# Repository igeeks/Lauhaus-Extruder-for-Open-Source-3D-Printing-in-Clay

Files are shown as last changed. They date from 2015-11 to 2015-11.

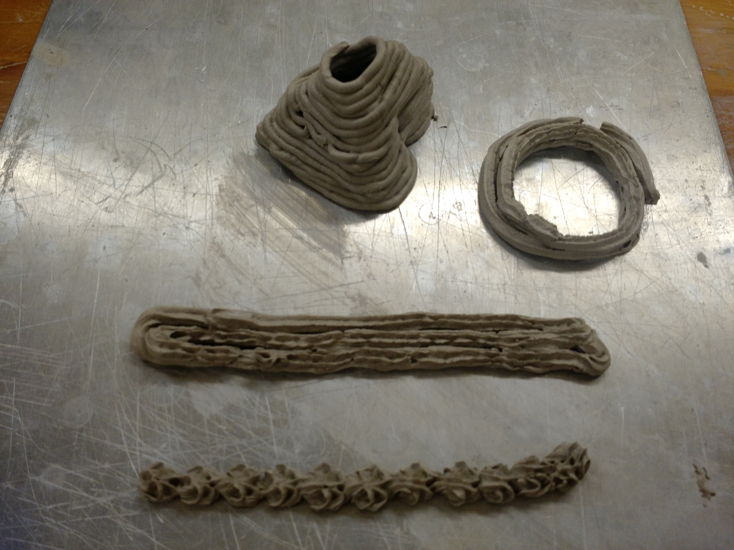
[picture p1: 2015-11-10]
Version 0.2_1 (uses Frosting Tip)/Images/IMG_20151110_134412253.jpg

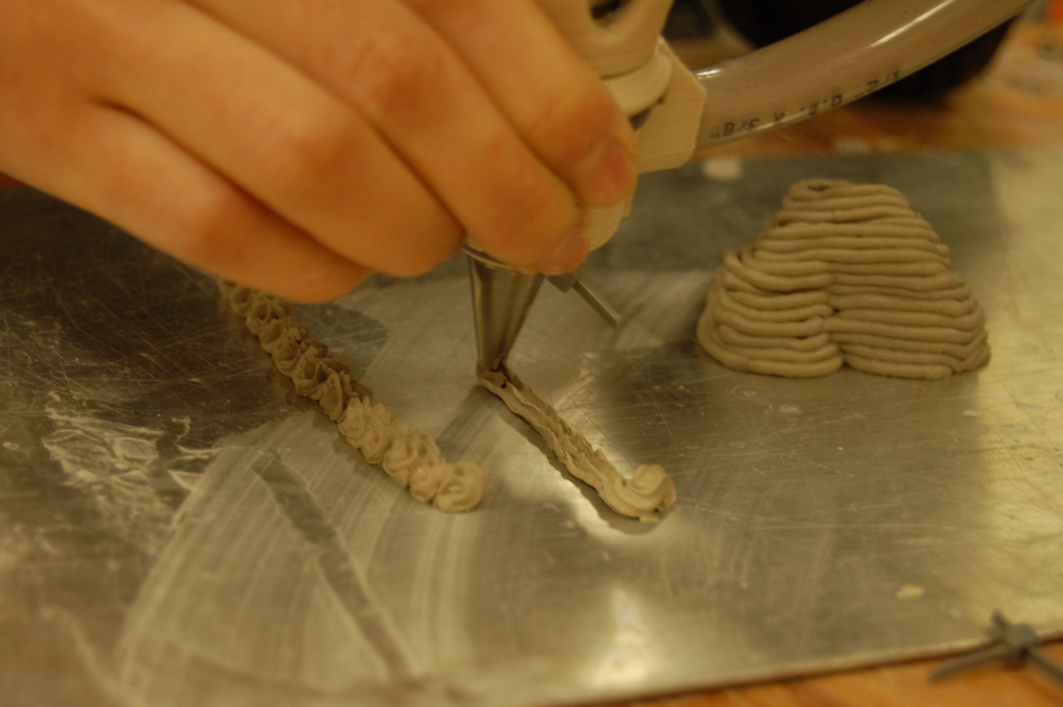
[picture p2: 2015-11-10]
Version 0.2_1 (uses Frosting Tip)/Images/DSC_0014.JPG

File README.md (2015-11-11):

# Lauhaus-Extruder-for-Open-Source-3D-Printing-in-Clay
An Open Source 3D print head for printing clay and perhaps other pastes & fluids

Fist of all, many thanks to people who have been pioneering open source 3d printing in clay. Notably Dries Verbruggen of Unfold Studio, Jonathan Keep of the "Build Your Own Ceramic Delta Printer", WASP Project - a 3D printer company based in Italy doing remarkable work, and Richard Horne "RichRap3D" whose open source paste extruder was the first RepRap clay extruder I came across.

The design here draws inspiration and conceptual direction from all of those individuals listed and some others too. This project is intended to be as low-cost as possible and also as easy to assemble and use as possible. It tries to be reliant on parts which are widely available or 3d printable. 

This project is being developed by students of Engineering and students of Art at Penn State University. The project receives support from Penn State's Learning Factory program: http://www.lf.psu.edu/ . The project is being led by Tom Lauerman, an artist & teacher with an interest in 3D printing, clay, design, engineering, bicycles, eating ice cream, playing drums poorly, and other activities. http://www.tomlauerman.com/

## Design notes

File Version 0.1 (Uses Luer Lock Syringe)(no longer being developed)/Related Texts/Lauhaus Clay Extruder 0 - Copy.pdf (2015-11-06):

## Lauhaus Clay Extruder 0.1 Bill of Materials

with helpful links and counterproductive observations

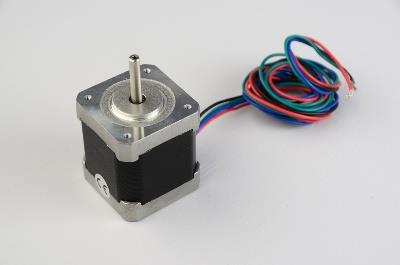
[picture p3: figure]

One Nema 17 Motor – the most common motor used in RepRap printers. Available in many locations. I buy mine from Lulzbot: https://www.lulzbot.com/products/nema-17-stepper-motor . These can also sometimes be found inside of old document scanners if you like breaking things.

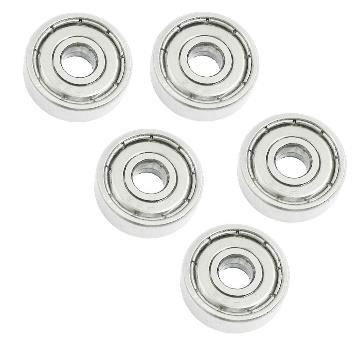
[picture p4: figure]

One 625ZZ Bearing 5mm x 5mm x 16mm – These are very common in skateboard wheels and are very cheap – usually less than 1 dollar per. Should be in stock at your local skate shop. Also at Amazon: http://www.amazon.com/Skateboard-Groove-Radial-Bearings-625ZZ/dp/B009EPNW8Y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 (http://www.amazon.com/Skateboard-Groove-Radial-Bearings-625ZZ/dp/B009EPNW8Y?s=industrial)

One wood screw. The first one I tried was 14 guage (1/4inch diameter (6.3mm metric)) and was three inches long. I cut the head off with a dremel cut off wheel. This screw worked, but I’m certain there ae better augers out there. I plan to experiment with a range of screws, drill bits, etc. Also I’m not sure why something labeled ¼” (6.3mm) was able to fit in the bearing’s 5mm hole. I sanded it a bit, but not that much. I think screws are highly variable by manufacturer and that their dimensions are sometimes more nominal than actual – at least in my neck of the woods. Here’s one similar to mine. (https://www.fastenal.com/products/details/1130238)

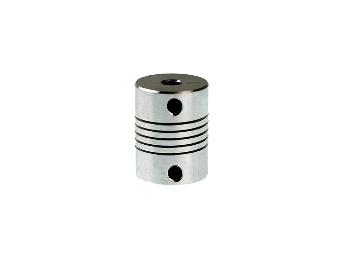
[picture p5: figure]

One flexible coupler. – 5mm holes – This attaches the screw to the motor shaft. These can be purchased online, here’s where mine came from. (https://www.inventables.com/technologies/flexible-coupler) That said, I always liked the way the Prusa i3 printer originally used a piece of tubing instead of a coupler. (http://3.bp.blogspot.com/-Z1Y2iyhLs8A/UhL_BsgxiFI/AAAAAAAAF6w/BmKeCiHRCiw/s1600/Prusai3-metalframe.jpg) So maybe this coupler is a bit too esoteric for my design – it may not be necessary – I’m going to try alternatives.

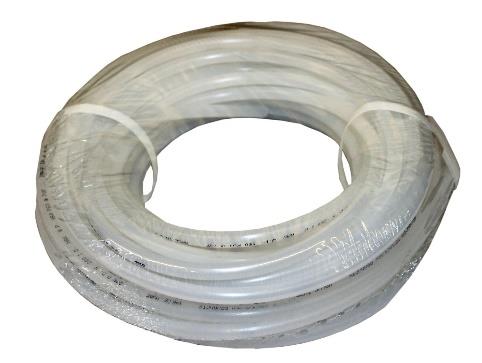
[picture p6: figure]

Flexible tubing (to from feed tank to extruder head) I used some that had an inside diameter of 3/8” and an outside diameter of ½”. The WASP project uses 12mm tubing, which I’m guessing is essentially the exact same diameter. I used regular plastic tubing from the local hardware store. This was a bad choice! The WASP project uses Teflon (ptfe) tubing – which I’m sure significantly reduces drag on the clay moving through the tube. I’m going to buy some Teflon tube from here. (http://www.mcmaster.com/#5033k35/=zp269m) Actually, on second thought, that is annoyingly expensive tubing. I may go over to the part of my campus where the cows are kept and milked (hundreds of them) and ask around about what type of tubing has the least friction. Then I’m going to get Ice Cream.

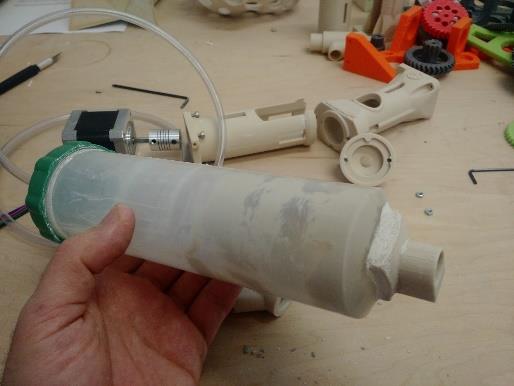
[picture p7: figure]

Clay holding/Feed tank. I repurposed this one from the Jonathan Keep printer bill of materials. I cut off the luer lock syringe tip, drilled the hole out to ½ inch and 3d printed anew nozzle fitting for it which I epoxied on with PC-11 epoxy. This is not an ideal solution! I mean it worked fine, but its smallish and why buy a thing just to cut it up and glue printed parts to? Look how nice the WASP project tank is (lower right):

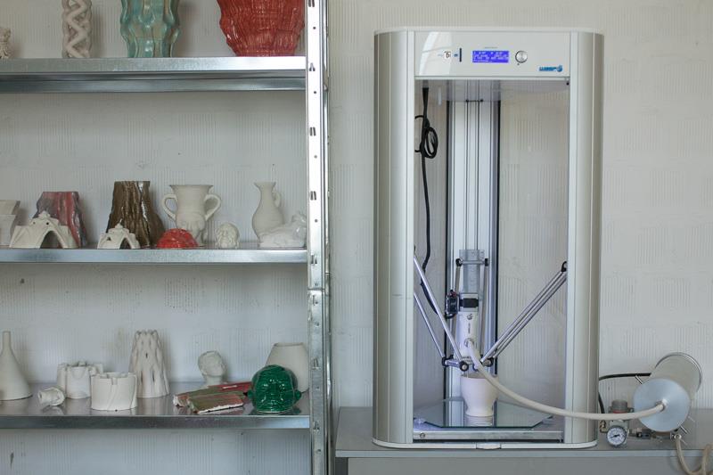
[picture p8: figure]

That said, I actually have a grudge against the pneumatic holding tank aspect of the project. I really want to design and build a mechanical tank – a stepper motor driven plunger. For two reasons:

1. To be able to modulate feed rate and pressure via software/firmware.
2. Air compressors are expensive, large, and noisy.

More on this later – but eliminating all compressed air from the system is a goal of mine.

That’s everything (+ the three 3d printed parts (extruder shell, extrude cap, part that does the work).

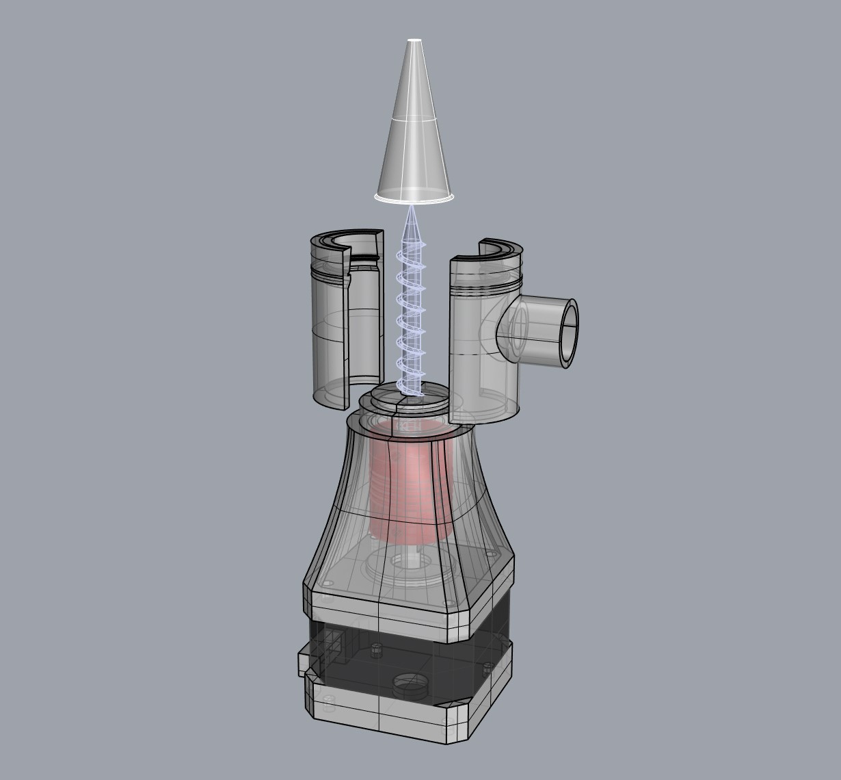
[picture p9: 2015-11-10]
Version 0.2_1 (uses Frosting Tip)/Images/Clay Extruder 02.jpg

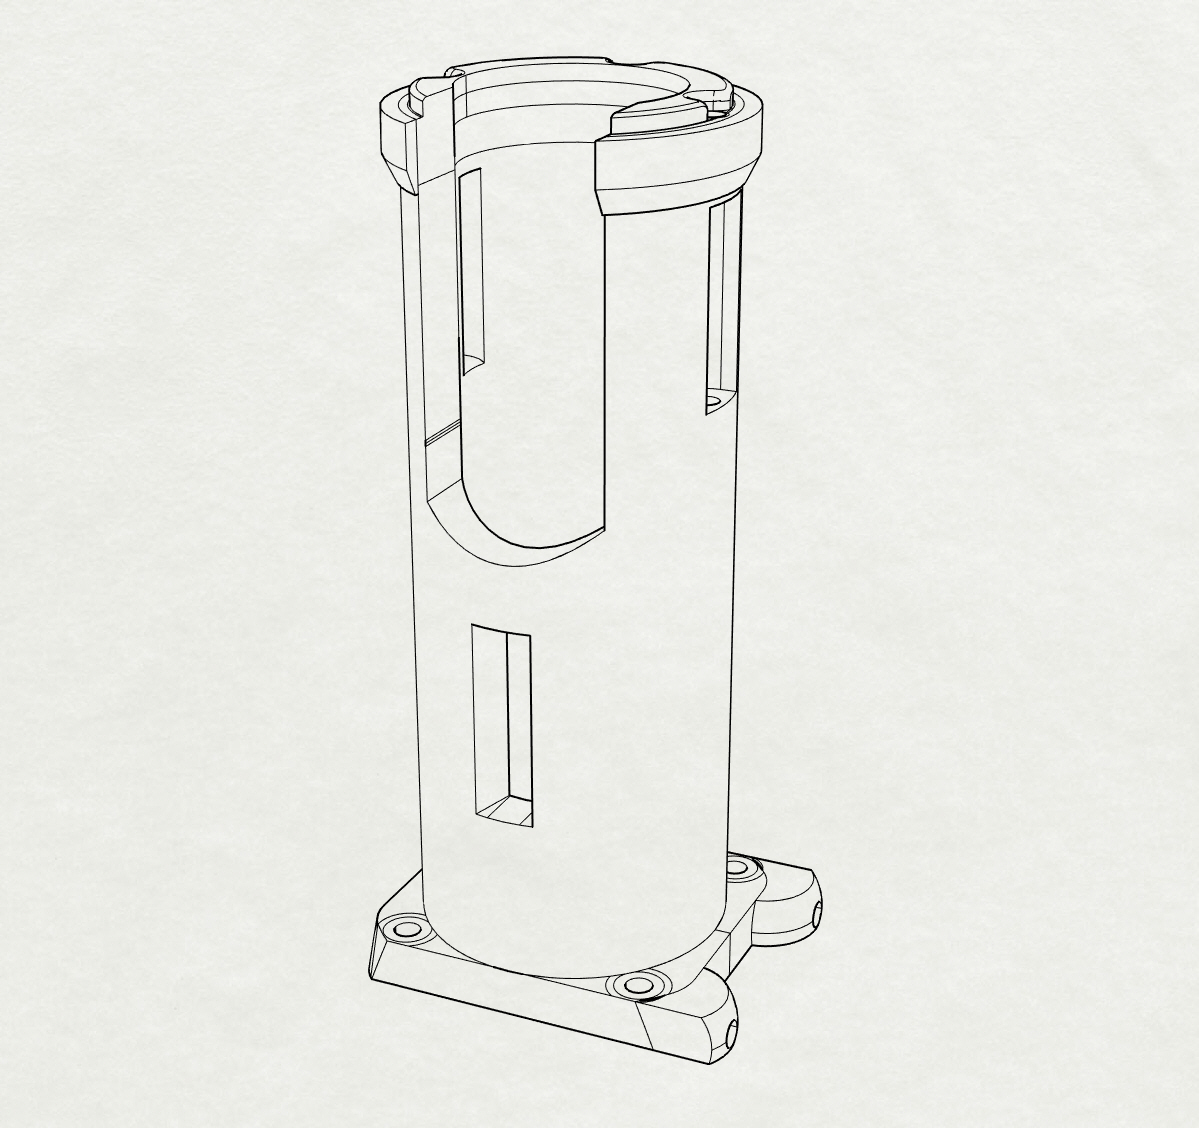
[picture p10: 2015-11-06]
Version 0.1 (Uses Luer Lock Syringe)(no longer being developed)/JPG Files/Lauhaus Extuder Shell.jpg

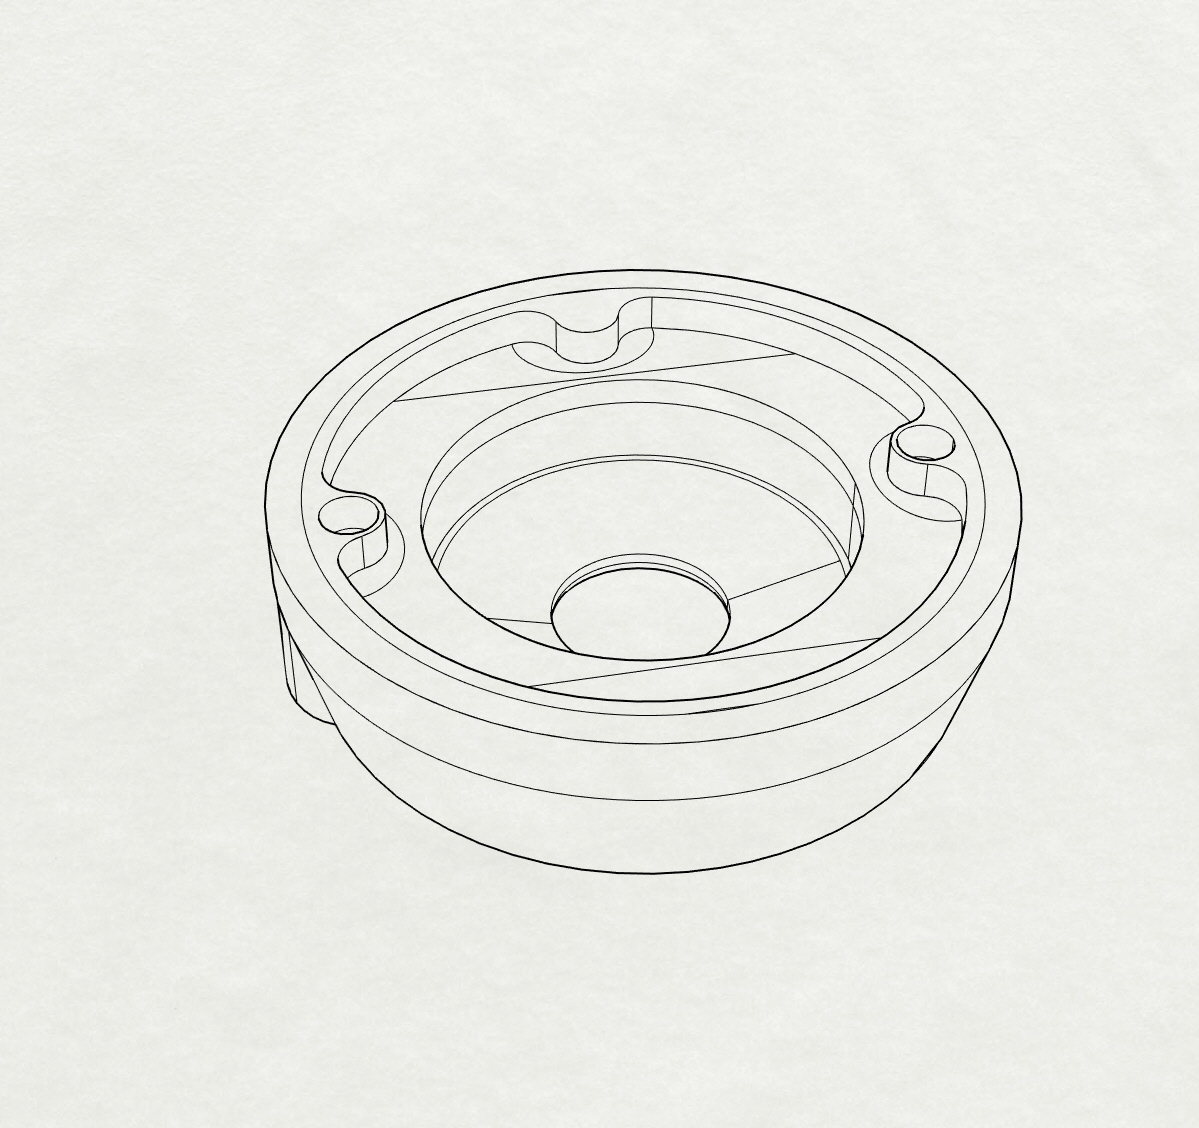
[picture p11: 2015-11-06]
Version 0.1 (Uses Luer Lock Syringe)(no longer being developed)/JPG Files/Lauhaus Extuder Cap.jpg

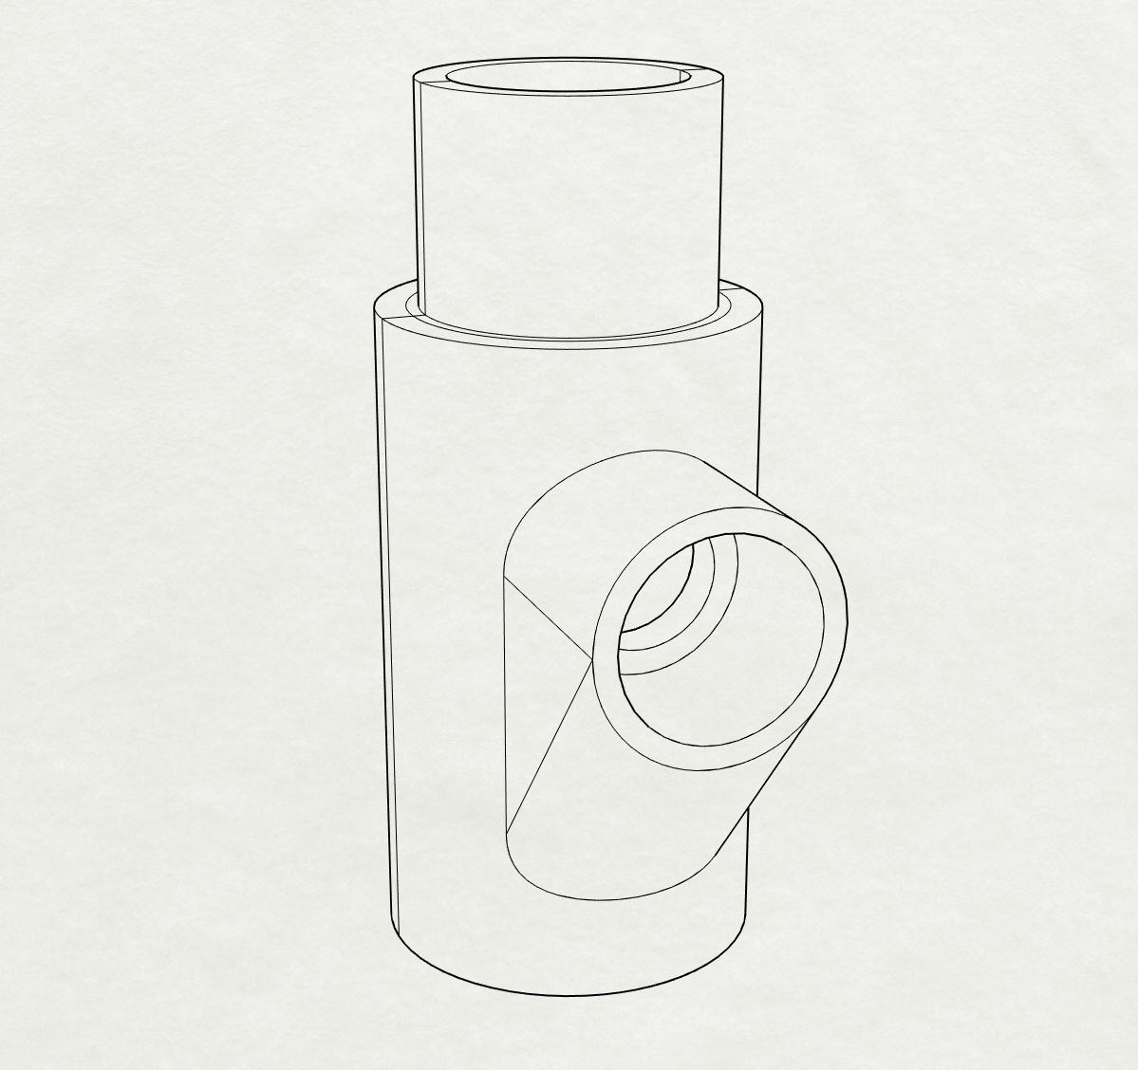
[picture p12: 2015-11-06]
Version 0.1 (Uses Luer Lock Syringe)(no longer being developed)/JPG Files/Lauhuas Extruder Part Which Does The Work.jpg

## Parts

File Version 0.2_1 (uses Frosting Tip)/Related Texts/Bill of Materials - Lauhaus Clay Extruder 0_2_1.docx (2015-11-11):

Lauhaus Clay Extruder 0.2_1 Bill of Materials

with helpful links and counterproductive observations

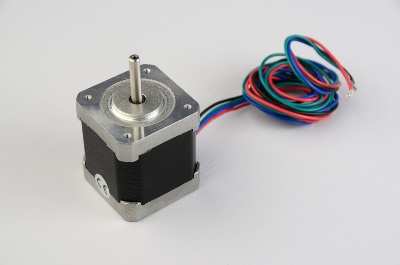
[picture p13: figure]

$13.95

One Nema 17 Motor – the most common motor used in RepRap printers. Available in many locations. I buy mine from Lulzbot: https://www.lulzbot.com/products/nema-17-stepper-motor . These can also sometimes be found inside of old document scanners if you like breaking things.

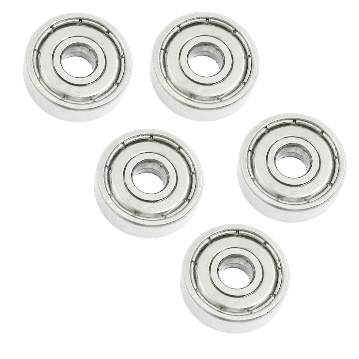
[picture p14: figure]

$1.00 (approx.)

One 625ZZ Bearing 5mm x 5mm x 16mm – These are very common in skateboard wheels and are very cheap – usually less than 1 dollar per. Should be in stock at your local skate shop. Also at Amazon: http://www.amazon.com/Skateboard-Groove-Radial-Bearings-625ZZ/dp/B009EPNW8Y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

$0.69

One screw. I used a “Timber Tite ¼” x 4” Deck Screw I purchased from my local hardware store. I cut the head off using a Dremel cut-off wheel. http://wedo.hillmangroup.com/item/all-categories/timbertite-trade-landscape-screw/47804

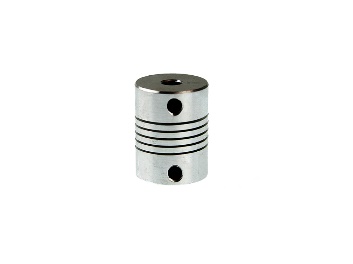
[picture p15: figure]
Flexible Coupler

$2.99

One flexible coupler. – 5mm holes – This attaches the screw to the motor shaft. These can be purchased online, here’s where mine came from (https://www.inventables.com/technologies/flexible-coupler). Here’s a cheaper that I’m sure works just as well (http://www.ebay.com/itm/Flexible-Shaft-Coupler-5mm-To-5mm-CNC-Mill-Router-Reprap-Prusa-i3-3D-printer-/121485418717). That said, I always liked the way the Prusa i3 printer originally used a piece of tubing instead of a coupler (http://3.bp.blogspot.com/-Z1Y2iyhLs8A/UhL_BsgxiFI/AAAAAAAAF6w/BmKeCiHRCiw/s1600/Prusai3-metalframe.jpg). So maybe this coupler is a bit too esoteric for my design – it may not be necessary – I’m going to try alternatives.

Total extruder cost: $18.63

Feed System Items

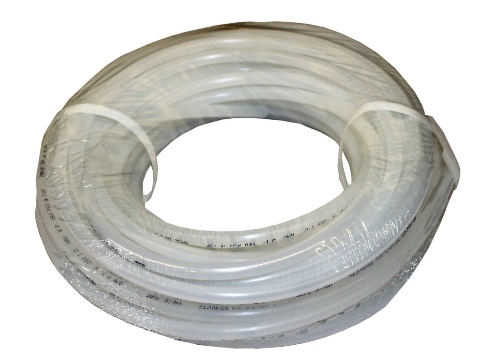
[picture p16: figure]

Flexible tubing (to from feed tank to extruder head) I used some that had an inside diameter of 3/8” and an outside diameter of ½”. The WASP project uses 12mm tubing, which I’m guessing is essentially the exact same diameter. I used regular plastic tubing from the local hardware store. This was a bad choice! The WASP project uses Teflon (ptfe) tubing – which I’m sure significantly reduces drag on the clay moving through the tube. I’m going to buy some Teflon tube from here (http://www.mcmaster.com/). Actually, on second thought, that is annoyingly expensive tubing. I may go over to the part of my campus where the cows are kept and milked (hundreds of them) and ask around about what type of tubing has the least friction. Then I’m going to get Ice Cream.

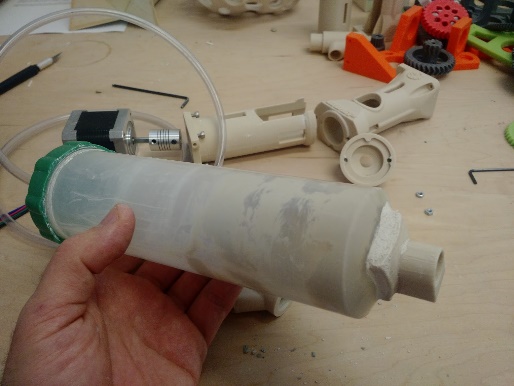
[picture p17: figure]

Clay holding/Feed tank. I repurposed this one from the Jonathan Keep printer bill of materials. I cut off the luer lock syringe tip, drilled the hole out to ½ inch and 3d printed anew nozzle fitting for it which I epoxied on with PC-11 epoxy. This is not an ideal solution! I mean it worked fine, but its smallish and why buy a thing just to cut it up and glue printed parts to? Look how nice the WASP project tank is (lower right):

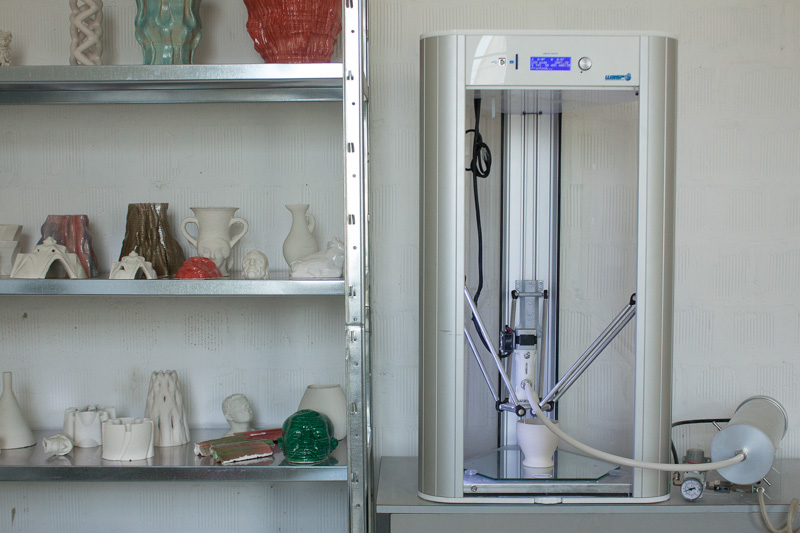
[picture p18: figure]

That said, I actually have a grudge against the pneumatic holding tank aspect of the project. I really want to design and build a mechanical tank – a stepper motor driven plunger. For two reasons:

1. To be able to modulate feed rate and pressure via software/firmware.
2. Air compressors are expensive, large, and noisy.

More on this later – but eliminating all compressed air from the system is a goal of mine.

That’s everything (+ the three 3d printed parts (extruder shell, extrude cap, part that does the work).

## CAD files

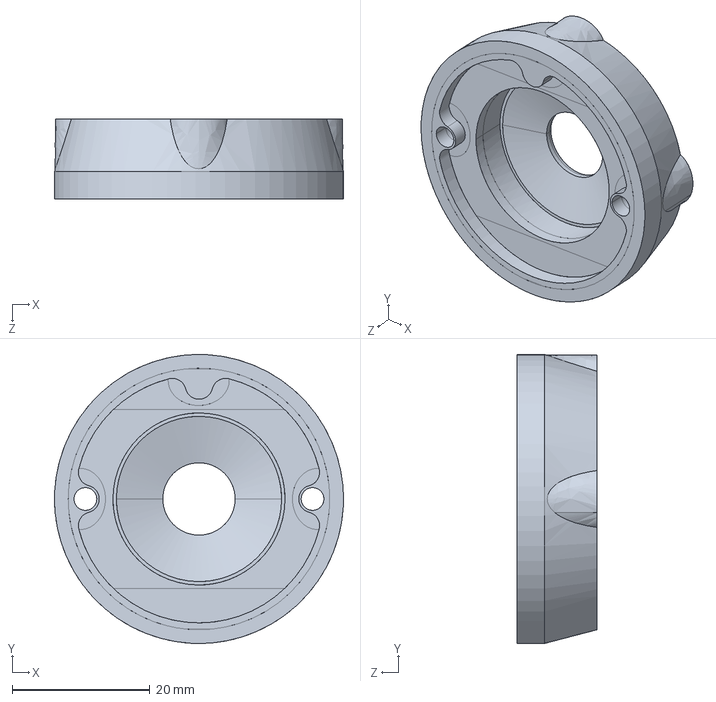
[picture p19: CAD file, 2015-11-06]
Version 0.1 (Uses Luer Lock Syringe)(no longer being developed)/IGES Files/Lauhaus Extruder Cap.igs
42.0 x 42.0 x 11.7 mm

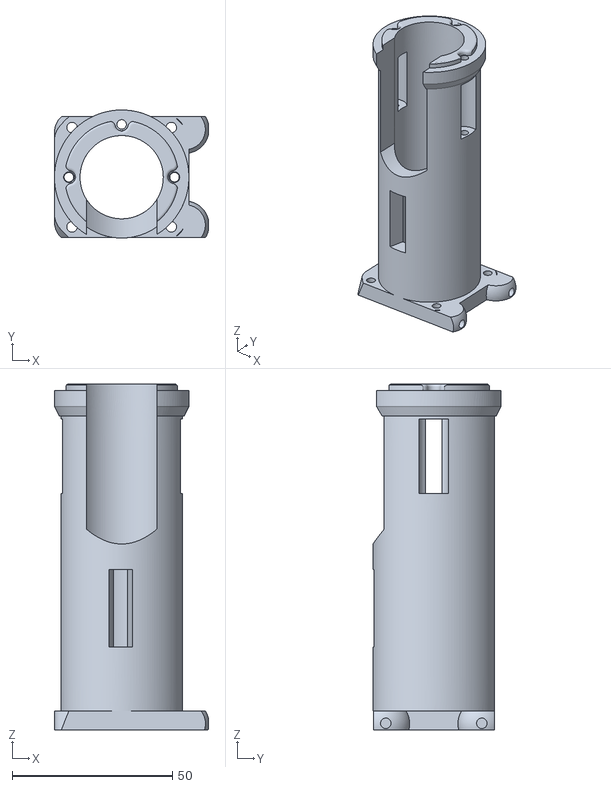
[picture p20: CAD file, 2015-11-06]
Version 0.1 (Uses Luer Lock Syringe)(no longer being developed)/STL Files/Lauhaus Extruder Shell.stl
48.1 x 40.0 x 108.1

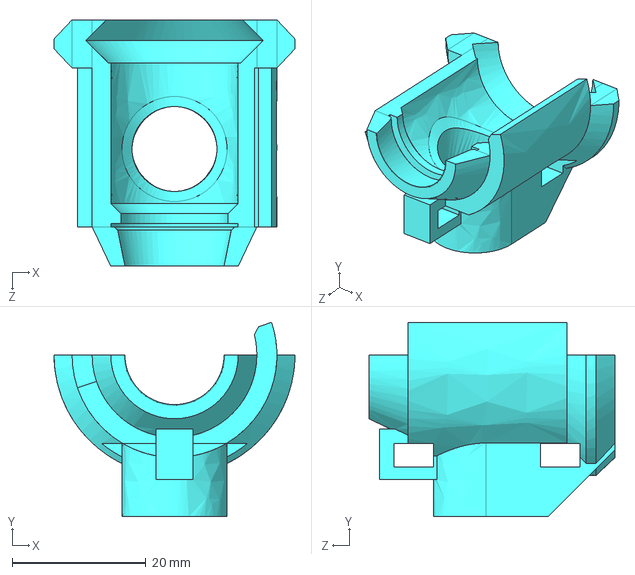
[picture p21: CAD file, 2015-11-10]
Version 0.2_1 (uses Frosting Tip)/IGES Files/Lauhaus Clay Extruder Side A 0_2_1.igs
36.0 x 29.1 x 36.9 mm

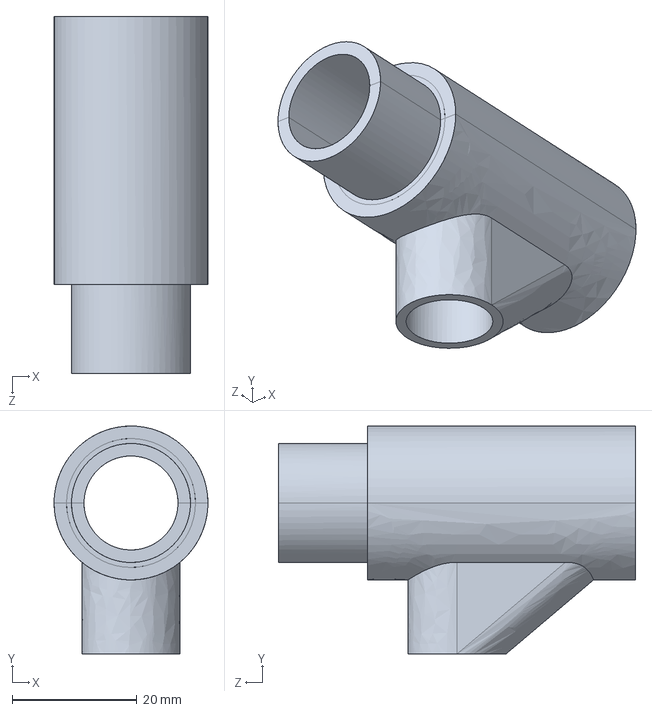
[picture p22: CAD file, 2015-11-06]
Version 0.1 (Uses Luer Lock Syringe)(no longer being developed)/IGES Files/Lauhaus Extruder Part Which Does The Work.igs
24.6 x 36.5 x 57.2 mm

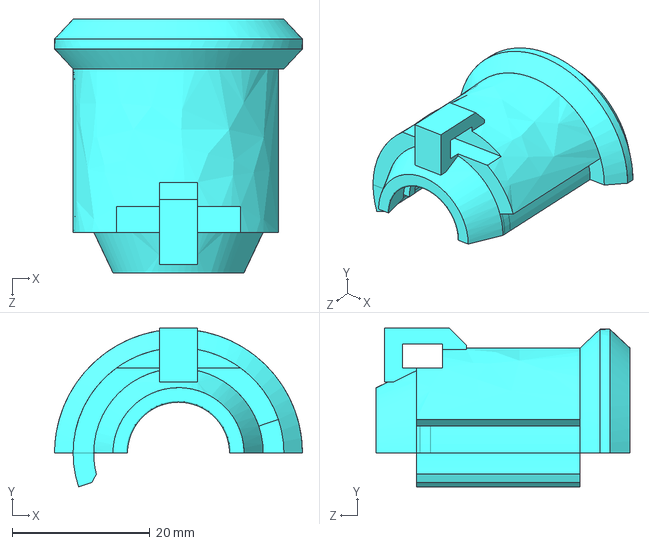
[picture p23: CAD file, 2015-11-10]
Version 0.2_1 (uses Frosting Tip)/IGES Files/Lauhaus Clay Extruder Side B 0_2_1.igs
36.0 x 23.1 x 36.9 mm

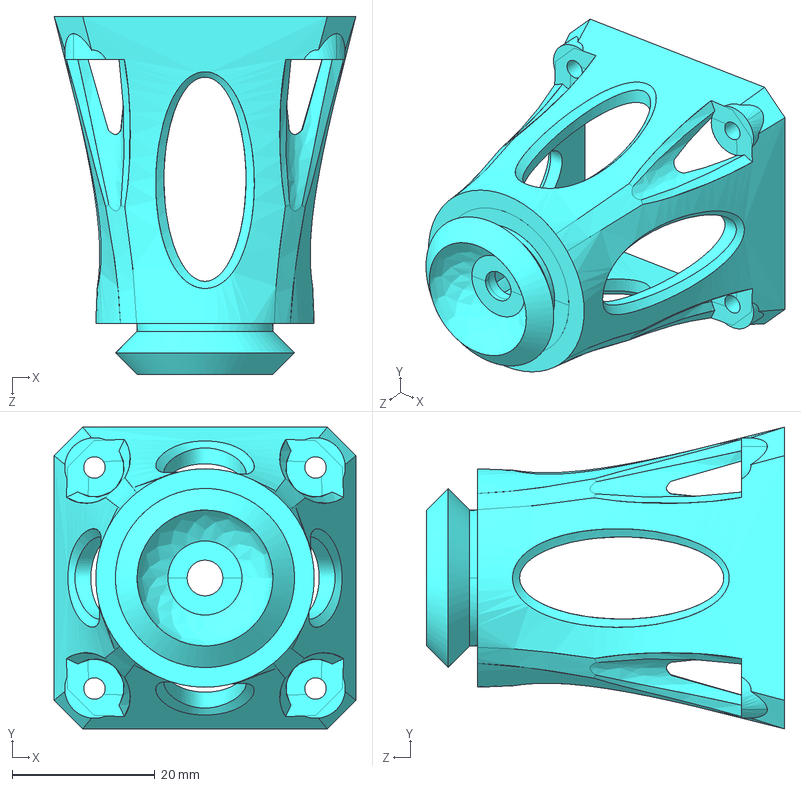
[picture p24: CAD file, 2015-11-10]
Version 0.2_1 (uses Frosting Tip)/IGES Files/Lauhaus Clay Extruder Base 0_2_1.igs
42.3 x 42.3 x 50.2 mm

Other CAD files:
Version 0.1 (Uses Luer Lock Syringe)(no longer being developed)/IGES Files/Lauahaus Extuder Shell.igs
Version 0.1 (Uses Luer Lock Syringe)(no longer being developed)/Rhino Files/Lauhaus Extruder Cap.3dm
Version 0.1 (Uses Luer Lock Syringe)(no longer being developed)/Rhino Files/Lauhaus Extruder Part Which Does The Work.3dm
Version 0.1 (Uses Luer Lock Syringe)(no longer being developed)/Rhino Files/Lauhaus Extuder Shell.3dm
Version 0.1 (Uses Luer Lock Syringe)(no longer being developed)/STL Files/Lauhaus Extruder Cap.stl
Version 0.1 (Uses Luer Lock Syringe)(no longer being developed)/STL Files/Lauhaus Extruder Part Which Does The Work.stl
Version 0.2_1 (uses Frosting Tip)/Rhino Files/Lauhaus Clay Extruder Base.3dm
Version 0.2_1 (uses Frosting Tip)/Rhino Files/Lauhaus Clay Extruder mixing chamber side A.3dm
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

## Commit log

2015-11-06 IGS file for the lauhaus extruder cap
    The cap holds the contents of the extruder inside the shell.
    [Lauhaus Cap.3dm, Lauhaus Cap.igs, Lauhaus Cap.stl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]
2015-11-06 Revert "IGS file for the lauhaus extruder cap"
    This reverts commit bdfdb1c1f903752fdcb1ec13b0975c68df08d4e5.
    [Lauhaus Cap.3dm, Lauhaus Cap.igs, Lauhaus Cap.stl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]
2015-11-06 CAD files of the three printed parts in the extruder design
    These are the CAD files, suitable for 3d printing
    [Lauhaus Extruder Cap.stl, Lauhaus Extruder Part Which Does The Work.stl, Lauhaus Extruder Shell.stl]
2015-11-06 Rhino Files for the Extruder
    I model in Rhino primarily. Therefore these are my primary design files.
    [Lauhaus Extruder Cap.3dm, Lauhaus Extruder Part Which Does The Work.3dm, Lauhaus Extuder Shell.3dm]
2015-11-06 IGES Files for the Extruder
    These files are in the IGES format (Initial Graphics Exchange Format).
    Seems like a good format for programs like Solidworks (which I do not
    use often)
    [Lauahaus Extuder Shell.igs, Lauhaus Extruder Cap.igs, Lauhaus Extruder Part Which Does The Work.igs]
2015-11-06 Images of the CAD files for reference
    Here's what these parts look like (at least onscreen)
2015-11-06 Added Bill Of Materials
    William (of materials)
2015-11-06 Added PDF BOM
    .
2015-11-06 Revert "Added PDF BOM"
    This reverts commit 41da92c009078710de265b27dc76fe37d10350ba.
2015-11-06 Revert "Added Bill Of Materials"
    This reverts commit 2109b47e45110012944dddccbf2f68b46c7280be.
2015-11-06 Revert "Revert "Added Bill Of Materials""
    This reverts commit 74675736ea140597e4e65bfe7e759e3e9d291cd5.
2015-11-06 Revert "Revert "Revert "Added Bill Of Materials"""
    This reverts commit 5b6758276b9928b750ccc79bab713245ccbff3e2.
2015-11-10 RhinoFiles for Version 0.2_1
    These are entirely new parts and dimensions. Drawn 'from scratch" by Tom
    Lauerman - November 2015
    [Lauhaus Clay Extruder Base.3dm, Lauhaus Clay Extruder mixing chamber side A.3dm, Lauhaus Clay Extruder mixing chamber side B.3dm]
2015-11-10 Rhino File Folder
    Rhino File Folder added
    [Lauhaus Clay Extruder Base.3dm, Lauhaus Clay Extruder mixing chamber side A.3dm, Lauhaus Clay Extruder mixing chamber side B.3dm]
2015-11-10 Added IGES and STL Files for Version 0.2_1
    more files
    [Lauhaus Clay Extruder Base 0_2_1.igs, Lauhaus Clay Extruder Base 0_2_1.stl, Lauhaus Clay Extruder Side A 0_2_1.igs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]
2015-11-10 Images and things added
    more pictures
    [Lauahaus Extuder Shell.igs, Lauhaus Extruder Cap.3dm, Lauhaus Extruder Cap.igs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]
2015-11-10 nomenclature changes
    etc
    [Lauahaus Extuder Shell.igs, Lauhaus Extruder Cap.3dm, Lauhaus Extruder Cap.igs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]
2015-11-11 added 2_0_1 Bill Of Materials
    William, Of Materials
